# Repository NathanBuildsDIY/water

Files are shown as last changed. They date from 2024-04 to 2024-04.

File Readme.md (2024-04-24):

This is the installation files for a robot waterer that feeds from a rain barrel. Learn more at the youtube link here:

To set up your raspberry pi zero w

If you log in via ssh and it hangs, improve ssh response times with this command and then reboot: echo "IPQoS cs0 cs0" | sudo tee -a /etc/ssh/sshd_config

install git on your raspberry pi: sudo apt-get -y install git

clone this git repository to your pi home directory: git clone https://github.com/NathanBuildsDIY/water.git

Run initial setup: nohup sh water/initial-setup.sh & Note - you can watch the output with: tail -f nohup.out

Connect to the new wifi hostpot called rain. Visit http://rain.local/run to control your watering robot. 

You can still ssh to the waterer (while connected to the rain wifi) via ssh or putty

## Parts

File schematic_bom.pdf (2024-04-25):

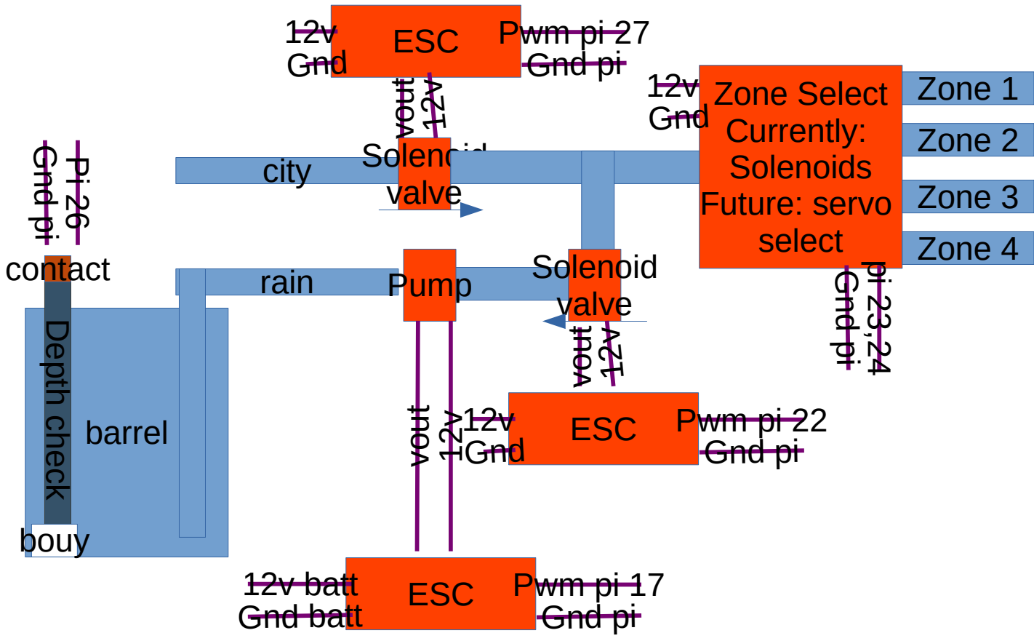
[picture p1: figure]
city; barrel; c h e c k bouy; contact; rain; Solenoid valve; Solenoid valve Pump; 12v batt; ESC Gnd batt; Pwm pi 17 Gnd pi; Zone Select Currently: Solenoids Future: servo select; Zone 1 Zone 2; Zone 3 Zone 4; ESC Gnd; Pwm pi 22 Gnd pi; ESC; Gnd; Pwm pi 27 Gnd pi; 12v Gnd

Dc buck 12v batt
Gnd batt

5V
gnd

Pi Zero
2 W

17-pump
22-rain solenoid
23 – zone 1
24 – zone 2
27 – city solenoid

WLAN: water Pass: LetsWater URL: water.local

BOM - $186

Raspberry Pi Zero 2 W - $15 Micro SD – 32GB -$7
Package of wires – 18 gauge/header wires - $10

PETG for Case - $15
Solar panel & regulator - $30 https://www.amazon.com/TP-solar-Monocrystalline-Controller-Extension-Terminal/dp/B07RZBVTGR LiFEP04 battery – 10Ah - $35

Pump - $20
https://www.amazon.com/VerRich-diaphragm-Priming-Sprayer-Camper/dp/B08C4SM5QC Solenoid - $5 * 4 = 20
https://www.adafruit.com/product/997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 ESCs - $9 5 pack
Misc hose fittings/couplings/Tee - $25

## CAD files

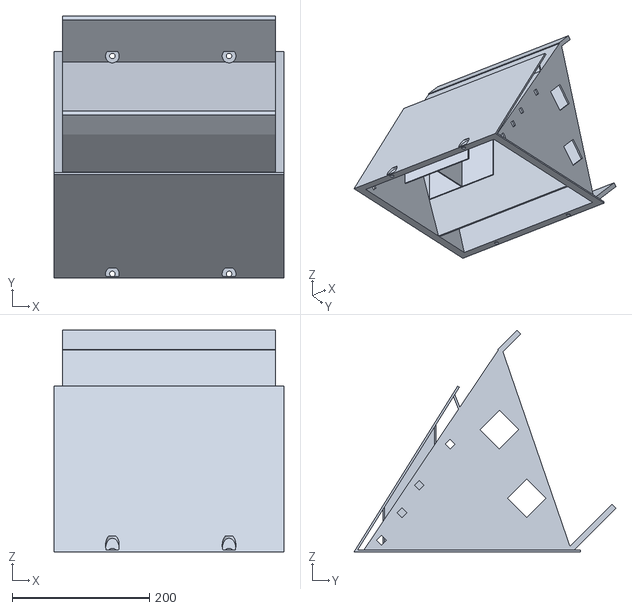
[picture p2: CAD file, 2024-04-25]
rain_v1.stl
335.0 x 381.8 x 323.3

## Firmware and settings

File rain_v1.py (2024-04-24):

#TO DO: Ensure short enough watering time and non conflict on water times (separate by at least a minute)
#TO DO: add /static/css/style.css and make it look pretty
#TO DO: Allow /time to also set day of week. radio button, convert to date/year/month.  Show what day it thinks it is now
#TO DO: read crontab to get current program even after loss of power
#TO DO: add USB dongle to get time/date even when power is lost
#TO DO: resize panel/battery to not lose power
#TO DO: sense when barrel is out. switch to city supply (route around pump)
#TO DO: Create BOM

import os
from glob import glob
import time
from datetime import datetime, date
#make the web app work
from flask import Flask, render_template, redirect, url_for
from flask_wtf import FlaskForm
from wtforms import (IntegerField, SelectField, RadioField)
from wtforms import widgets, SelectMultipleField
from wtforms.validators import InputRequired, Length
from wtforms.fields import DateField, TimeField
from flask_autoindex import AutoIndex
from crontab import CronTab
import getpass

zones=2 #create arrays below beyond 2, up to 16. But this limits how many we print. Zone 0 is not used.
savedMinute=[0,0,0,0,0,0,0,0,0,0,0,0,0,0,0,0]
savedHour=[0,0,0,0,0,0,0,0,0,0,0,0,0,0,0,0]
savedRuntime=[0,0,0,0,0,0,0,0,0,0,0,0,0,0,0,0,0]
savedDays=["","","","","","","","","","","","","","","",""]

def createCrons(days,startTime,endTime,zone):
  print("creating crons now")
  cron = CronTab(user=getpass.getuser())
  runTime=datetime.combine(date.today(), endTime) - datetime.combine(date.today(), startTime)
  runTimeSeconds=int(runTime.total_seconds())
  print("run Time is: ",str(runTimeSeconds))
  #daysFormatted="'"+"', '".join(days)+"'"
  daysFormatted="', '".join(days)
  print("days are: ",daysFormatted)
  print("minutes are: ",startTime.minute," hours are: ",startTime.hour)
  #min hour * * day,day,day command
  job = cron.new(command="python3 ~/water/water_v1.py --seconds "+str(runTimeSeconds)+" --zone "+str(zone), comment="Watering Zone "+str(zone))
  job.minute.on(str(startTime.minute))
  job.hour.on(str(startTime.hour))
  for dow in days:
    job.dow.also.on(dow)
  cron.write()
def deleteCrons():
  #cron below not working. try os instead
  user=getpass.getuser()
  os.system("crontab -u "+user+" -l | grep -v 'Watering Zone'  | crontab -u "+user+" -")
  #cron = CronTab(user=getpass.getuser())
  #for job in cron:
  #  print(job)
  #  jobText=str(job)
  #  if 'Watering Zone' in jobText:
  #    print("removing old cron: ",job)
  #    cron.remove( job )
  #cron.remove_all('water_v1.py')
  #cron.remove_all(comment='Watering Zone')
def readCrons():
  global savedMinute, savedHour, savedDays, savedRuntime, zones
  cron = CronTab(user=getpass.getuser())
  jobs = cron.find_command('water/water')
  index = 1
  for job in jobs:
    jobText=str(job)
    jobTextArray=jobText.split()
    savedMinute[index]=str(job.minute)
    savedHour[index]=str(job.hour)
    savedDays[index]=str(job.dow)
    savedRuntime[index]=str(jobTextArray[8])
    index = index + 1
def resetCurrentTime(currentTime):
  print("Setting system time to: ",currentTime.strftime("%H:%M"))
  date_cmd = 'sudo date --set=\"20240410 '+str(currentTime.hour)+':'+str(currentTime.minute)+'\"'
  print("Command: "+date_cmd)
  os.system(date_cmd)

SECRET_KEY = 'rainkey'
app = Flask(__name__)

app.config.from_object(__name__)
class MultiCheckboxField(SelectMultipleField):
    widget = widgets.ListWidget(prefix_label=False)
    option_widget = widgets.CheckboxInput()
class rainForm(FlaskForm):
    days1 = MultiCheckboxField('Days', choices=[('MON','Mon'),('TUE','Tue'),('WED','Wed'),('THU','Thu'),('FRI','Fri'),('SAT','Sat'),('SUN','Sun')])
    startTime1 = TimeField('Start Time', format='%H:%M')
    endTime1 = TimeField('End Time', format='%H:%M')
    days2 = MultiCheckboxField('Days', choices=[('MON','Mon'),('TUE','Tue'),('WED','Wed'),('THU','Thu'),('FRI','Fri'),('SAT','Sat'),('SUN','Sun')])
    startTime2 = TimeField('Start Time', format='%H:%M')
    endTime2 = TimeField('End Time', format='%H:%M')
class timeForm(FlaskForm):
	currentTime = TimeField('Current Time', format='%H:%M') #took out - problems: , default=datetime.now().strftime("%H:%M:%S")

@app.route('/',methods=['post','get'])
def run():
  global savedMinute, savedHour, savedRuntime, savedDays, zones, job1, job2
  form = rainForm()
  if form.validate_on_submit():
    print("Raw input values are:")
    print(form.days1.data)
    print(form.startTime1.data)
    print(form.endTime1.data)
    print(form.days2.data)
    print(form.startTime2.data)
    print(form.endTime2.data)
    #Check for errors and do the work
    deleteCrons()
    createCrons(form.days1.data,form.startTime1.data,form.endTime1.data,1)
    createCrons(form.days2.data,form.startTime2.data,form.endTime2.data,2)
  else:
    print(form.errors)
  readCrons()
  return render_template('rain.html',datetime = str(datetime.now().strftime("%H:%M")),
    savedDaysTem1=str(savedDays[1]),savedStartTimeTem1=str(savedHour[1])+":"+str(savedMinute[1]),savedRuntimeTem1=str(savedRuntime[1]),
    savedDaysTem2=str(savedDays[2]),savedStartTimeTem2=str(savedHour[2])+":"+str(savedMinute[2]),savedRuntimeTem2=str(savedRuntime[2]),form=form)

@app.route('/time',methods=['post','get'])
def time():
  form = timeForm()
  if form.validate_on_submit():
    print("Raw input values are:")
    print(form.currentTime.data)
    #Check for errors and do the work
    resetCurrentTime(form.currentTime.data)
  else:
    print(form.errors)
  return render_template('time.html',datetime = str(datetime.now().strftime("%H:%M")),form=form)

if __name__ == '__main__':
  app.run(debug=True)

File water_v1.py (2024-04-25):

from gpiozero import Device, PhaseEnableMotor, Robot, PhaseEnableRobot, LED, Servo, AngularServo, Button, PWMLED
#from gpiozero.pins.pigpio import PiGPIOFactory
import datetime
import time

import argparse
parser = argparse.ArgumentParser()
parser.add_argument("--seconds", help="Number of seconds to turn on pump",type=int, default="10")
parser.add_argument("--zone", help="Zone to turn on =",type=int, default="1")
args = parser.parse_args()

#factory = PiGPIOFactory()
#pump = AngularServo(10, initial_angle=0, min_angle=0, max_angle=180, min_pulse_width=4/10000, max_pulse_width=25/10000,pin_factory=factory)
#pump = PWMLED(12, initial_value = 0, pin_factory = factory) #only if factory works - pi zero

cityWater = LED(27)
rainWater = LED(22)
rainBarrelFull = Button(26)
pump = LED(17)
if args.zone == 1:
  zoneValve = LED(23)
if args.zone == 2:
  zoneValve = LED(24)
  
now = datetime.datetime.now()
print("starting pump now for these seconds: ",args.seconds)
print(now)
#pump.blink(on_time=args.seconds,off_time=1,fade_in_time=1,fade_out_time=1)
#pump.blink(1,1,1,1,2,True)
zoneValve.on()
time.sleep(0.5) #let valve open before we pump
if rainBarrelFull.is_pressed:
  rainWater.on()
  time.sleep(0.5)
  pump.on()
  time.sleep(args.seconds)
  pump.off()
  time.sleep(0.5)
  rainWater.off()
else:
  cityWater.on()
  time.sleep(args.seconds)
  cityWater.off()
  time.sleep(0.5)
zoneValve.off()
now = datetime.datetime.now()
print("turning off pump now for zone: ",args.zone)
print(now)

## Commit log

2024-04-17 Add files via upload
    update pins on watering to avoid pumps turning on during startup
    [water_v1.py]
2024-04-24 Update initial-setup.sh
    fix paths, reduce power
2024-04-25 Add files via upload
    3d printer file and schematic/bom
    [rain_v1.stl]
